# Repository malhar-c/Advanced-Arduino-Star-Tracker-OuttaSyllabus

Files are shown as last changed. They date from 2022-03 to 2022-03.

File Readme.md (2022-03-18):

# DIY Advanced Star Tracker with Arduino and NEMA 17 (A4988)

> ***Author:** Malhar Chakraborty (OuttaSyllabus)*

> ***Date:** 18/03/2022*

> ***Started Advanced version:** Oct 2021 (See the Release notes)*

> ***Started Barn door tracker Arduino project:** *Dec 2020* [GitHub Link](https://github.com/malhar-c/Star-Tracker-ver.-11.x.x)*

________
> **Features:**
>  - 0 Manual mechanical operation.
>  - Auto calibration after startup and end of track using limit switches this results in higher total track time by using the whole
> length of the threaded rod.
>  - Auto correct tangent error overtime (using variable speed stepper drive) calculation is done using length from the hinge to threaded rod
> and the pitch of the threaded rod used.
>  - Low noise operation (using 16th micro-stepping)
>  - Non-blocking stepper driving using timer interrupts (library)
>  - Lots of customization options for future.

## Electronics:

 1. Arduino Nano
 2. A4988 Stepper Driver
 3. NEMA 17 Stepper (1.8 step angle) Motor
 4. 4x4 Matrix Membrane keypad with I2c module (LCD backpack)
 5. 1602 LCD with I2c backpack
 6. Analog Temperature sensors (thermistors)
 7. Fan (12V)
 8. MOSFET (IRFP150 or any n-channel mosfet will work) for Fan control
 9. KA7805 (5v Voltage regulator for Arduino voltage supply)
 10. Power source: 18650 Li ion cells (3s) with 3s BMS
 11. Capacitive Touch sensor for shake free operation of the tracker. `Note: this didn't work for me as everytime the modules stop working for some reason, but would be a very nice addition.`
 12. Limit switches (for upper and lower limit detection and calibration)

> **Note:** I've used a diode as temperature sensor as I ran out of thermistors and I was rushing to finish the initial prototype, it worked and I left it as it is, probably have to replace in future, as it's not as accurate and it depends on a ref voltage, which surprisingly in my case varies when I use the external power source, and when I use USB to power the Arduino only (it's not usable when used with USB as temp readings are incorrect).

## Mechanical construction and Hardware:

### Barndoor construction

> Watch the YouTube video for details about the construction and working :- [Coming soon @OuttaSyllabus](https://www.youtube.com/c/OuttaSyllabus)
> **NOTE:** Here I've listed the dimensions I've used in my design, you can vary everything as long as functionality is met.

 - Ply wood planks (about 11 inches long and) x2 `Note: I've used some lying around pieces of ply woods, any hardwood should work as long as you can work with it. xD`
 - Hinges x2 to make the barn door (2 inches)

### Tracking and mounting
> Link(s) I followed for construction:
>
> [Swivel mount design](https://www.nutsvolts.com/magazine/article/january2015_Wierenga)
>
> [f/138 – Daniel Berrangé](https://fstop138.berrange.com/2014/01/building-an-barn-door-mount-part-1-arduino-stepper-motor-control/)
>
> [Barn door tracker Calculator](https://blarg.co.uk/astronomy/barn-door-tracker-calculator)

1. PVC pipes cut to the breadth of the planks (1 inch dia) x2
2. PVC pipe holders (1 inch dia) x4

> **Note:** To this PVC pipe the motor and threaded rod mechanism will be attached such that it will swivel as the barn door opens with time.

4. Threaded rod (1mm pitch 5mm dia) `any dimensions will work just remember we have to couple this to the shaft of NEMA 17 and we need to know the pitch precisely because based on that only the tracking algorithm will work.`
5. Tee nut and washers.
6. NEMA 17 clamp `we have to attach the NEMA 17 to one of those PVC pipes so pick a Clamp which will work in this situation, I've just used a L bracket as nothing was available except of that. For more details watch the YT video @OuttaSyllabus`
7. NEMA 17 Shaft coupler.
8. Ball Head with suitable mounting hardware (to mount the ball had on top of the plank which will hold the camera).
9. Extra tripod quick release plate `You probably can skip this. I ordered one extra QR plate and permanently attached it to the barn door with two part resin epoxy adhesive (or whatever it's called, I've used Araldite) as my tracker was quite heavy and I though it would be more secure with this approach, you just need some sort of arrangement to mount it on top of a tripod without any wiggle room.`

### Electronics/Controls housing

> 3D Printed enclosure, printed in ABS+ (The A4988 heats up easily to around 50C without proper cooling, the ABS can survive up to 80-90 deg C direct contact with the heatsink, thus enough headroom.)

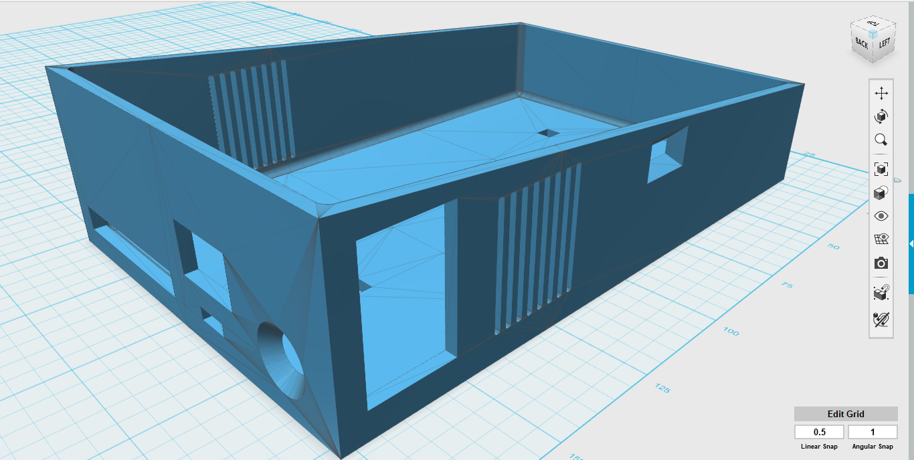
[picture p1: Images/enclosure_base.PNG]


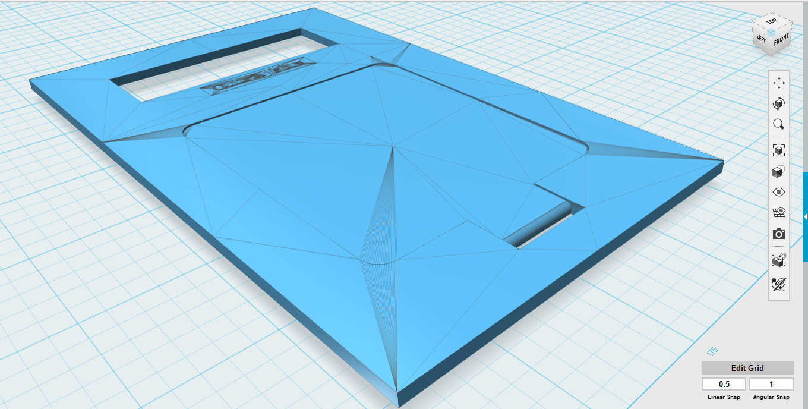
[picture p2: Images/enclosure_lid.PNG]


## Exact components used (Links):

 1. Arduino: [Nano CH340 Chip Board without USB cable compatible with Arduino (Soldered)](https://robu.in/product/arduino-nano-board-r3-with-ch340-chip-wo-usb-cable-solderedarduino-nano-r3-wo-usb-cable-soldered/)
 2. A4988: [A4988 driver Stepper Motor Driver- Good Quality](https://robu.in/product/a4988-driver-stepper-motor-driver/)
 3. Stepper Motor shaft coupler: [Aluminum Flexible Shaft Coupling 5mm x 5mm](https://robu.in/product/aluminium-flexible-shaft-coupling-5mm-x-5mm/)
 4. 4x4 Membrane keypad: [# 4?4 Matrix Keypad Membrane Switch for Arduino, ARM and other MCU](https://robu.in/product/4x4-matrix-keypad-membrane-switch-arduino-arm-mcu/)
 5. 1602 LCD : [LCD1602 Parallel LCD Display Yellow Backlight](https://robu.in/product/serial-lcd1602-iic-i2c-yellow-backlight/)
 6. I2c backpack : [IIC/I2C Serial Interface Adapter Module](https://robu.in/product/iici2c-serial-interface-adapter-module/)
 7. Analog Temperature sensors (thermistors) : [Analog Temperature Sensor Module](https://robu.in/product/analog-temperature-module/)
 8. Fan (12V) : [12V 3010 Cooling Fan for 3D Printer](https://robu.in/product/12v-3010-cooling-fan-for-3d-printer/)
 9. KA7805 : [KA7805 Linear Voltage Regulator (Pack of 3 Ics)](https://robu.in/product/ka7805-linear-voltage-regulator-pack-of-3-ics/)
 10. 3s BMS: [3 Series 20A 18650 Lithium Battery Protection Board 11.1V 12V 12.6V](https://robu.in/product/3-series-20a-18650-lithium-battery-protection-board-11-1v-12v-12-6v/)
 11. Capacitive touch sensor: [Digital Sensor TTP223B Module Capacitive Touch Switch](https://robu.in/product/digital-sensor-ttp223b-module-capacitive-touch-switch/)
 12.

## Pin configurations

### Stepper Motor Driver (A4988)

> **Note:** These configurations will be directly done to the library file. Follow this link for more details about the library used: [Library for A4988 stepper motor driver using timer interrupt](https://www.programming-electronics-diy.xyz/2017/10/library-for-a4988-stepper-motor-driver.html)

> You have to define these pins using port register manipulation to increase read/write speeds. Read more about *Arduino port manipulation* [here](https://electronoobs.com/eng_arduino_tut130.php)

| A4988 Pin |  Arduino PIN|
|--|--|
| Step | Digital 9 |
| Dir  |  Digital 8  |
| Sleep | Digital 13 |
| MS1 | Digital 12 |
| MS2 | Digital 11 |
| MS3 | Digital 10 |

### Other accessories
| Accessory PIN |  Arduino PIN|
|--|--|
| A4988 Thermistor | Analog 7 |
| KA7805 Diode temp sensor  |  Analog 2  |
| Fan MOSFET (Gate) | Digital 3 |
| Lower Limit Switch (Pulled up) | Digital 4 |
| Upper Limit Switch (Pulled up) | Digital 2 |
| Touch switch | Digital 7 |

> **NOTE:** LCD and matrix keypad both are used using LCD i2c backpacks (just because they are cheap) but these backpacks have a minor problem which resulted in one of the rows of my keypad not working (just throwing random inputs when pressed) that didn't bother me though as I didn't need all 16 inputs, and this is easily fixable by going with a proper i2c module (which just happens to be 3-4 times more expensive in my area than the LCD backpack).

> Watch this for info: [Want to use a Keypad in your Arduino projects but running out of Pins?](https://youtu.be/n9Bq1kHYsJk)

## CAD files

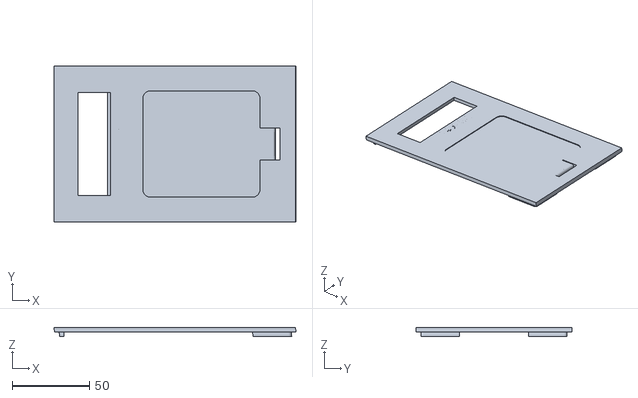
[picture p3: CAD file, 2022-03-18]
3d Models/enclosure lid top side facing up.stl
157.0 x 101.0 x 6.03

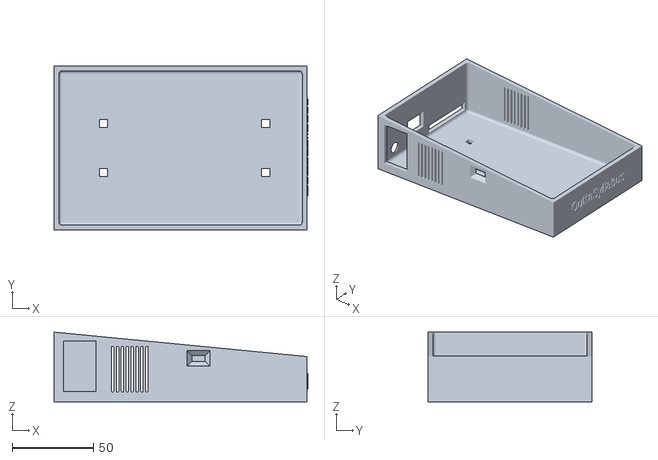
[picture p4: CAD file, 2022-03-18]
3d Models/enclosure base only.stl
156.5 x 101.0 x 43.0

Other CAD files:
3d Models/enclosure lid bottom side facing up.stl

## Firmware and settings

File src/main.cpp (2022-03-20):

#include <arduino.h>
#include <Keypad_I2C.h>
#include <LiquidCrystal_I2C.h>
#include <Keypad.h>
#include <Wire.h>

//stepper control with timer interrupts implementation
//all settings are done in library (pinouts, microstepping threasholds, etc)
#include <avr/io.h>
#include "A4988-stepperDriver.h"
#include <util/delay.h>

#define max_steps 12500 //25000

//siderial tracking calculations [all in mm and minutes]
#define SIDEREAL_DAY_MINUTES      1436.06818333  //1436.06818333 minutes
#define THREAD_PITCH              1   //1mm pitch
#define SWIVEL_MOUNT_DISTANCE     21  //21mm
#define BASE_RADIUS_AT_0_DEG      256   //radius when the planks are at 0 degree = 256mm

float theta = 0;
float psi = 0;
float correction = 0;

//I2C devices
#define I2CADDR 0x26 //keypad
#define I2CLCDADDR 0x27 //lcd

//Thermistor/Diode & Fan PINs
#define A4988_Thermistor A7
#define KA7805_Diode_Sensor  A2 // used to bias the diode  anode
#define fanPin 3

//Stopper switches
#define Lower_Limit 4
#define Upper_Limit 2

//TouchPad
#define Touch_pad 7
#define Touchpad_enable 0   //  0=false 1=true

const byte ROWS = 4; //four rows
const byte COLS = 4; //four columns

char hexaKeys[ROWS][COLS] =
{
  {'0','*','7','4'},
  {'4','0','8','5'},
  {'6','#','9','6'},
  {'C','D','C','B'}
};

byte rowPins[ROWS] = {4, 5, 6, 7};
byte colPins[COLS] = {3, 2, 1, 0};

//initialize an instance of class NewKeypad
Keypad_I2C customKeypad(makeKeymap(hexaKeys), rowPins, colPins, ROWS, COLS, I2CADDR);

//iniliatize lcd
LiquidCrystal_I2C lcd(I2CLCDADDR,16,2);   //16 02 LCD

//Temperaure calculation variables
int Vo;
float R1 = 10000;
float logR2, R2, T, Tc;
float c1 = 1.009249522e-03, c2 = 2.378405444e-04, c3 = 2.019202697e-07;
//diode temp cal
const int t0 = 20.3;        // calibration temp
const float vf0 = 573.44;   // measured forward voltage
float dtemp;
float dtemp_avg;
float t;
float greater_temp = 0;  //stores the higher temp value among the components

//other Variables
bool low_lim_flag = 0;
bool up_lim_flag = 0;
bool calib_flag = false; //once the calibation is done this should be true
bool track_flag = false;
bool manual_flag = false;
bool fan_man_flag = false;
long StepCount = 0;
bool Touch_1 = 0;
bool LCD_backlight_flag = true;
short fan_speed = 0;
unsigned long curr_temp_disp_millis = 0;
unsigned long prev_temp_disp_millis = 0;
short temp_disp_state = 0;
unsigned long curr_millis = 0;
unsigned long prev_millis = 0;
bool fan_auto_on = 0;
unsigned long arduino_runtime_millis = 0;
float solar_time = 0;
float sidereal_time = 0;
const float sidereal_conv = 1.0/0.99726958;
unsigned long delay_bet_steps_us = 0;


//siderial tracking variables
static long startPositionUSteps;
static long startPositionSecs;
static long startWallClockSecs;

static long targetWallClockSecs;
static long targetPositionSecs;
static long targetPositionUSteps;

//LCD functions
void starting_text();
void calibrating_text();
void ready_text();
void temp_display();
void Track_text();
void turn_on_backlight();


//temp control functions
void update_temp();

//Star tracker functions
void Calibrate();
void Track();
void Track_end();
void Rewind();
void update_everything();
void Touch_pad_refresh();
void update_limit_switches(); //only limit switches or update eveyrithing
void manual_mode();
void runfan(int);
void temp_Fan_speed_control();
void Full_cycle();

unsigned long cal_sidereal(int);     //all the sidereal tracking calculations will be done here
float stepCount_to_seconds(long);

void setup()
{
  pinMode(Lower_Limit, INPUT_PULLUP);
  pinMode(Upper_Limit, INPUT_PULLUP);
  pinMode(fanPin, OUTPUT);
  pinMode(Touch_pad, INPUT);
  pinMode(KA7805_Diode_Sensor, INPUT_PULLUP); // set the  pin IN with npull up to bias the diode

  A4988_stepperSetup();

  Wire.begin();
  lcd.init();

  //show on the LCD
  starting_text();
  customKeypad.begin();
  Serial.begin(115200);

}

char customKey = customKeypad.getKey();

void loop()
{
  arduino_runtime_millis = millis();
  update_everything();
  Serial.println("inside loop");
  //ready_text();
  temp_display();
  temp_Fan_speed_control();
  runfan(fan_speed);

  if (Touch_1 && !track_flag)
  {
    goto track_init;
  }

  //bypass for debugging
  while(!calib_flag)
  {
    calibrating_text();
    Calibrate();
  }

  while(track_flag)
  {
    Track();
  }

  while(manual_flag)
  {
    manual_mode();
  }

  //turn_on_backlight();

  customKey = customKeypad.getKey();
  switch(customKey)
  {
    case 'B':
    track_init: //for the touch control to directly trigger track
    Serial.println("inside case B");
    //delay(1000);
    lcd.clear();
    lcd.home();
    lcd.print("B. Start Track");
    lcd.setCursor(0,1);
    lcd.print("*. Back");
    // delay(1000);
    Touch_pad_refresh();
    customKey = customKeypad.getKey();
    while(customKey != 'B' || customKey != '*')
    {
      Touch_pad_refresh();
      customKey = customKeypad.getKey();
      if (customKey == '*')
      {
        ready_text();
        break;
      }
      if (customKey == 'B' || Touch_1)
      {
        track_flag = true;
        break;
      }
    }
    break;

    case 'C':
    lcd.clear();
    lcd.home();
    lcd.print("C. Rewind & Calib");
    lcd.setCursor(0,1);
    lcd.print("*. Back");
    customKey = customKeypad.getKey();
    while(customKey != 'C' || customKey != '*')
    {
      customKey = customKeypad.getKey();
      if (customKey == '*')
      {
        ready_text();
        break;
      }

      if (customKey == 'C')
      {
        calib_flag = false;
        break;
      }
    }
    break;

    case 'D':
    lcd.clear();
    lcd.home();
    lcd.print("D. Manual Conrol");
    lcd.setCursor(0,1);
    lcd.print("*. Back");
    Touch_pad_refresh();
    customKey = customKeypad.getKey();
    while(customKey != 'D' || customKey != '*')
    {
      Touch_pad_refresh();
      customKey = customKeypad.getKey();
      if (customKey == '*')
      {
        ready_text();
        break;
      }

      if (customKey == 'D')
      {
        manual_flag = true;
        break;
      }
    }
    break;

    //fan on off
    case '5':
    lcd.clear();
    lcd.home();
    if(fan_speed != 100)
    {
      fan_man_flag = true;
      fan_speed = 100;
      lcd.print("Fan: Man");
    }
    else
    {
      fan_man_flag = false;
      fan_speed = 0;
      lcd.print("Fan: Auto");
    }
    lcd.setCursor(0,1);
    temp_display();
    break;

    //reduce fan speed
    case '4':
    lcd.clear();
    lcd.home();
    fan_speed-=20;
    fan_man_flag = true;
    if(fan_speed <= 0)
    {
      fan_man_flag = false;
      fan_speed = 0;
    }
    lcd.print("Fan: Man (");
    lcd.print(fan_speed);
    lcd.print("%)");
    lcd.setCursor(0,1);
    temp_display();
    break;

    //increase fan speed
    case '6':
    lcd.clear();
    lcd.home();
    fan_speed+=20;
    fan_man_flag = true;
    if(fan_speed >= 100)
    {
      fan_speed = 100;
    }
    lcd.print(" Fan: Man (");
    lcd.print(fan_speed);
    lcd.print("%)");
    lcd.setCursor(0,1);
    temp_display();
    break;

    //backlight on/off
    case '8':
    {
      if(LCD_backlight_flag){
        LCD_backlight_flag = false;
      }
      else{
        LCD_backlight_flag = true;
      }
      break;
    }

    //full cycle (plank up and down)
    case '#':
    lcd.clear();
    lcd.home();
    lcd.print("#. Continue");
    lcd.setCursor(0,1);
    lcd.print("*. Back");
    Touch_pad_refresh();
    customKey = customKeypad.getKey();
    while(customKey != '#' || customKey != '*')
    {
      Touch_pad_refresh();
      customKey = customKeypad.getKey();
      if (customKey == '*')
      {
        ready_text();
        break;
      }

      if (customKey == '#')
      {
        Full_cycle();
        break;
      }
    }
    break;
  }
}

void Full_cycle()
{
  lcd.clear();
  lcd.print("Going up! ZoooO!");
  temp_Fan_speed_control();
  runfan(fan_speed);
  update_everything();
  //Serial.println("outside do");

  A4988_stepperWakeUp();
  //run motor to open plank
  A4988_stepperDirection(TURN_RIGHT);
  do
  {
    // Serial.println("inside do");

    A4988_stepMicroseconds(1, 1000);
    A4988_isBusy();
    StepCount+=1;
    update_limit_switches();
  }while(up_lim_flag != 1 && StepCount < max_steps);
  A4988_isBusy();
  A4988_stepperSleep();
  lcd.clear();
  lcd.print("Total: ");
  lcd.print(StepCount);
  lcd.setCursor(0,1);
  for(int i=0; i<16; ++i)
  {
    lcd.print(".");
    _delay_ms(250);
  }
  calib_flag = false;
}

void turn_on_backlight()
{
  if(LCD_backlight_flag)
  {
    lcd.backlight();
  }
  else
  {
    lcd.noBacklight();
  }
}

void starting_text()
{
  lcd.clear();
  //lcd.noBacklight();
  lcd.setCursor(2,0);
  lcd.print("Star Tracker");
  lcd.setCursor(4,1);
  lcd.print("ADVANCED");
}

void calibrating_text()
{
  lcd.clear();
  //lcd.backlight();
  lcd.setCursor(0, 0);
  lcd.print("Calibrating...");
  lcd.blink_on();
}

void ready_text()
{
  lcd.clear();
  lcd.setCursor(5, 0);
  lcd.print("READY!");
}

// void Track_text()
// {
//   lcd.setCursor(1, 0);
//   lcd.print("Tracking ");
//   lcd.print(StepCount);
// }

void temp_display()
{
  update_temp();
  lcd.setCursor(0, 1);
  lcd.print("R-");
  lcd.print(int(t));
  // lcd.print(" ");
  lcd.print((char)223);
  lcd.print(" ");
  lcd.print("D-");
  lcd.print(int(Tc));
  lcd.print((char)223);
  lcd.print(" ");
  lcd.print(fan_speed);
  lcd.print("%");
}


void update_temp()
{
  //A4988 temp calculation
  Vo = analogRead(A4988_Thermistor);
  R2 = R1 * (1023.0 / (float)Vo - 1.0);
  logR2 = log(R2);
  T = (1.0 / (c1 + c2*logR2 + c3*logR2*logR2*logR2));
  Tc = T - 273.15;

  //KA7805 temp calculation
  dtemp_avg = 0;
  for (int i = 0; i < 10; i++)
  {
    float vf = analogRead(KA7805_Diode_Sensor) * (4976.30 / 1023.000);
    dtemp = (vf - vf0) * 0.4545454;
    dtemp_avg = dtemp_avg + dtemp;
  }
  t = t0 - dtemp_avg / 10;
  if (t > (int)42)
  {
    LCD_backlight_flag = false;
  }

}

void temp_Fan_speed_control()
{
  //only if manual fan control is off
  if (!fan_man_flag)
  {
    //calculation of the greater temp among A4988 and KA7805
    if(Tc > t){
      greater_temp = Tc;
    }
    else if(t > Tc){
      greater_temp = t;
    }
    else{
      greater_temp = Tc;
    }

    //Setting fan speed for higher temp component
    if(greater_temp >= 37.00)
    {
      fan_auto_on = 1;
      //fan_speed = greater_temp;
      float speedf;
      speedf = (greater_temp-37.00) * (100.00-50.00) / (45.00-37.00) + 50.00;
      fan_speed = (int)speedf;
      // fan_speed = map(greater_temp, 37.00, 45.00, 50, 100);
    }
    else if (greater_temp < 33.00)
    {
      fan_speed = 0;
      fan_auto_on = 0;
    }

    if (fan_auto_on && greater_temp < 37.00)
    {
      float speedf;
      speedf = (greater_temp-33.00) * (100.00-30.00) / (45.00-33.00) + 30.00;
      fan_speed = (int)speedf;
    }
  }
}

void Calibrate()
{
  calib_flag = true;
  A4988_stepperWakeUp();
  //run motor to close plank
  A4988_stepperDirection(TURN_LEFT);
  // _delay_ms(500);
  do
  {
    A4988_stepMicroseconds(1, 1000);
    update_limit_switches();
  } while(low_lim_flag != 1);

  A4988_isBusy();
  _delay_ms(100);

  //run the motor to open the plank
  A4988_stepperDirection(TURN_RIGHT);
  do
  {
    A4988_stepMicroseconds(1, 1000);
    update_limit_switches();
  } while(low_lim_flag == 1);
  A4988_isBusy();
  _delay_ms(100);
  A4988_stepperSleep();
  // // [NO NEED] run motor to open plank a bit more for buffer
  // Set_RPM(150);
  // stepper.setMicrostep(1);
  // stepper.rotate(180);
  StepCount = 0;
  // stepper.disable();
  // delay(200);
  ready_text();
  temp_display();
}

void update_limit_switches()
{
  if(digitalRead(Lower_Limit) == 0){
    low_lim_flag = 1;
  }

  else{
    low_lim_flag = 0;
  }

  if(digitalRead(Upper_Limit) == 0){
    up_lim_flag = 1;
  }

  else{
    up_lim_flag = 0;
  }
}

void Touch_pad_refresh()
{
  if(Touchpad_enable)
  {
    Touch_1 = digitalRead(Touch_pad);
    // Serial.print("TouchPad debug status: ");
    // Serial.println(digitalRead(Touch_pad));
  }

  else
  {
    Touch_1 = 0;
  }
}

void update_everything()
{
  lcd.noBlink();
  turn_on_backlight();
  update_limit_switches();
  update_temp();
  Touch_pad_refresh();
}

void manual_mode()
{
  manual_flag = false;
  lcd.clear();
  lcd.noBlink();
  lcd.print("7. Open plank");
  lcd.setCursor(0,1);
  lcd.print("9. Close Plank    ");
  bool Open_toggle_state = false;
  bool Close_toggle_state = false;
  do
  {
    update_limit_switches();
    customKey = customKeypad.getKey();
    switch (customKey)
    {
      case '7':
      A4988_stepperWakeUp();
      if(Open_toggle_state == false){
        Open_toggle_state = true;
      }else{
        Open_toggle_state = false;
      }
      break;

      case '9':
      A4988_stepperWakeUp();
      //run motor to close plank
      if(Close_toggle_state == false){
        Close_toggle_state = true;
      }else{
        Close_toggle_state = false;
      }
      break;

      case '*':
      //delay(500);
      lcd.clear();
      lcd.print("Manual M Paused");
      lcd.setCursor(0, 1);
      lcd.print("#. Resm");
      lcd.print(" *. Cancl");
      // delay(500);
      do
      {
        customKey = customKeypad.getKey();
        if(customKey == '#')
        {
          lcd.clear();
          break;
        }
        else if (customKey == '*')
        {
          ready_text();
          temp_display();
          lcd.blink();
          A4988_stepperSleep();
          return;
        }
      } while(1);
    }
    if(Open_toggle_state)
    {
      //run motor to open plank
      A4988_stepperDirection(TURN_RIGHT);
      A4988_stepMicroseconds(1, 1000);
      A4988_isBusy();
      StepCount+=1;
      update_limit_switches();
      if(up_lim_flag || StepCount >= max_steps)
      {
        Open_toggle_state = false;
        lcd.clear();
        lcd.home();
        lcd.print("Upper Limit       ");
        //do something to tell the limit is reached
        _delay_ms(1000);
        update_limit_switches();
        lcd.clear();
        lcd.print("7. Open plank");
        lcd.setCursor(0,1);
        lcd.print("9. Close Plank    ");
      }
    }

    if(Close_toggle_state)
    {
      //run motor to close plank
      A4988_stepperDirection(TURN_LEFT);
      A4988_stepMicroseconds(1, 1000);
      A4988_isBusy();
      StepCount-=1;
      update_limit_switches();
      if(low_lim_flag)
      {
        Close_toggle_state = false;
        lcd.clear();
        lcd.home();
        lcd.print("Lower Limit       ");
        //do something to tell the limit is reached
        _delay_ms(1000);
        update_limit_switches();
        lcd.clear();
        lcd.print("7. Open plank");
        lcd.setCursor(0,1);
        lcd.print("9. Close Plank    ");
      }
    }
  } while(1);
}

void Track()
{
  float track_runtime = stepCount_to_seconds(StepCount);
  // Serial.print("TRACK RUNTIME: ");
  // Serial.println(track_runtime);
  track_flag = false;
  lcd.clear();
  lcd.print("Sid'eal Init");
  lcd.noBlink();
  LCD_backlight_flag = true;
  for(int i=0; i<4; i++)
  {
    _delay_ms(250);
    lcd.print(".");
  }
  lcd.setCursor(0, 1);
  // lcd.print("Remain': ~ ");
  // lcd.print(55 - (int)(track_runtime/60));
  // lcd.print("min");
  // _delay_ms(2000);
  //delay(500);
  LCD_backlight_flag = false;
  // temp_display();
  // lcd.clear();
  // Serial.println("track triggered");
  //tracking do
  do
  {
    solar_time = (float(millis() - arduino_runtime_millis)/1000) + track_runtime;
    sidereal_time = solar_time * sidereal_conv;
    update_everything();
    // Track_text();
    // temp_display();
    temp_Fan_speed_control();
    runfan(fan_speed);
    //update_limit_switches();
    //Touch_pad_refresh();
    customKey = customKeypad.getKey();
    //Serial.print(Touch_1);
    if (customKey == '*')// || Touch_1)
    {
      LCD_backlight_flag = true;
      lcd.clear();
      lcd.setCursor(1, 0);
      lcd.print("Tracking Paused");
      lcd.setCursor(0, 1);
      lcd.print("#. Resm");
      lcd.print(" *. Cancl");
      // delay(500);
      Touch_pad_refresh();
      customKey = customKeypad.getKey();
      do
      {
        Touch_pad_refresh();
        update_everything();
        temp_Fan_speed_control();
        runfan(fan_speed);
        customKey = customKeypad.getKey();
        if(customKey == '#' || Touch_1)
        {
          lcd.clear();
          LCD_backlight_flag = false;
          arduino_runtime_millis = millis();
          track_runtime = stepCount_to_seconds(StepCount);
          lcd.print("Sid'eal Tracking");
          break;
        }
        else if (customKey == '*')
        {
          A4988_stepperSleep();
          ready_text();
          temp_display();
          lcd.blink();
          return;
        }
      } while(1);
    }
    else if(customKey == '8')
    {
      if (LCD_backlight_flag)
      {
        LCD_backlight_flag = false;
      }
      else{
        LCD_backlight_flag = true;
      }
    }

    //Correcting the tangent error every 100 steps or half rotation
    if(StepCount%100 == 0)// || delay_bet_steps_us == 0)
    {
      //calculate the steps
      delay_bet_steps_us = cal_sidereal(sidereal_time);
      lcd.setCursor(0, 0);
      lcd.print("Remain': ~ ");
      lcd.print(55 - (int)(sidereal_time/60));
      lcd.print("min");
      temp_display();
    }
    A4988_stepperWakeUp();
    //run motor to open plank
    A4988_stepperDirection(TURN_RIGHT);
    // A4988_stepMilliseconds(1, delay_bet_steps_ms);
    A4988_stepMicroseconds(1, delay_bet_steps_us);
    Serial.println(StepCount);
    Serial.print(" DELAY BETWEEN Steps: ");
    Serial.println(delay_bet_steps_us);
    A4988_isBusy();
    StepCount+=1;

  }while(up_lim_flag != 1 && StepCount <= max_steps);
  Track_end();
}

void Track_end()
{
  bool lcd_blink_state = 0;
  A4988_stepperSleep();
  lcd.clear();
  lcd.print("Upper Limit");
  lcd.setCursor(0,1);
  lcd.print("C. Rewind & Calibrate");
  do
  {
    curr_millis = millis();
    if(curr_millis - prev_millis >= 1000)
    {
      prev_millis = curr_millis;
      if(!lcd_blink_state)
      {
        lcd.backlight();
        lcd_blink_state = 1;
      }
      else
      {
        lcd.noBacklight();
        lcd_blink_state = 0;
      }
    }

    // lcd.backlight();
    // lcd_blink_state = 1;
    // Stepper_beep();
    // delay(100);
    // lcd.noBacklight();
    // lcd_blink_state = 0;
    // delay(900);
    Touch_pad_refresh();
    customKey = customKeypad.getKey();
    Serial.print(Touch_1);
    //Serial.print(customKey);
    if(customKey == 'C' || Touch_1)
    {
      Serial.println("inside calibrate init");
      Serial.print(Touch_1);
      delay(500);
      calib_flag = false;
      Serial.print(Touch_1);
      break;
    }
  } while(customKey != '*' || !Touch_1);
  ready_text();
  temp_display();
}

//map(value, fromLow, fromHigh, toLow, toHigh)
void runfan(int speed)
{
  analogWrite(fanPin, map(speed, 0, 100, 100, 255));
  // Serial.print("Fan Speed Debug: ");
  // Serial.println(speed);
  if(speed == 0)
  {
    analogWrite(fanPin, 0);
  }
}

//Function for Siderial tracking calculations
unsigned long cal_sidereal(int track_sidereal_runtime)
{
  // short delay_steps_ms = 0;
  unsigned long delay_steps_us = 0; //changing the delay between steps calculation to us
  float Corrected_radius = 0;
  float Speed_in_RPM = 0;
  // Serial.print("Siderial RUNTIME: ");
  // Serial.print(track_sidereal_runtime);
  theta = (((float)track_sidereal_runtime)/3600) * (PI/12); //for max 1 hour
  // Serial.print(" Theta: ");
  // Serial.print(theta, 4);
  psi = (PI - theta)/2;
  // Serial.print(" PSI: ");
  // Serial.print(psi, 4);
  correction = SWIVEL_MOUNT_DISTANCE * tan((PI/2)-psi);
  // Serial.print(" Correction: ");
  // Serial.print(correction, 2);
  Corrected_radius = BASE_RADIUS_AT_0_DEG - correction;  //tangent error corrected bradius
  // Serial.print(" Corrected R: ");
  // Serial.print(Corrected_radius);
  Speed_in_RPM = Corrected_radius * ((2*PI)/SIDEREAL_DAY_MINUTES) * THREAD_PITCH;
  delay_steps_us = Speed_in_RPM*300000;
  // Serial.print(" RPM : ");
  // Serial.print(Speed_in_RPM);
  // Serial.print(" ");
  // Serial.print(delay_steps_us);
  return (delay_steps_us);
}

float stepCount_to_seconds(long steps)
{
  float rotations = (float)steps/200;
  float angle_rad = atan(rotations/BASE_RADIUS_AT_0_DEG);
  float angle_deg = angle_rad * (180/PI);
  float seconds = 240 * (angle_deg);
  // Serial.println(angle_rad, 6);
  // Serial.println(angle_deg);
  // Serial.println(seconds);
  // _delay_ms(5000);
  return (seconds);
}

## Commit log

2022-03-18 3d (printable) files added
    [enclosure base only.stl, enclosure lid bottom side facing up.stl, enclosure lid top side facing up.stl]
2022-03-19 diag Serial prints removed
2022-03-19 Fan Manual and Auto mode UI improved
2022-03-19 all custom 1602 characters removed (to cut complexity)
2022-03-20 track fn optimizations
2022-03-20 fan speed (%) addition beside temp display
2022-03-20 correct tan error every half rotation
    [main.cpp]
2022-03-20 Track resuming blank display fixed
    [main.cpp]
